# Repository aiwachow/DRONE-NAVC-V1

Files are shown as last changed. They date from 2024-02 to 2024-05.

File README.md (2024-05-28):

# NAVIGATION CONTROL SYSTEM - TEST BOARD 
STM32 based flight controller for unmanned drone aircraft. <br />
Created mainly for testing and learning to write firmware. 

I am simultaneously designing a newer version of this controller: branch NAVC_V2. 

## Board
SYSTEM_KONTROLI_LOTU
## Used software: 
kicadlogo stm32cubeideLOGOpythonLOGO

## Visualization 
I also made basic 3D attitude visualization in Python. 
dronPitch

dronRoll
### Some theory behind attitude estimation in Polish 
[Attitude_Estimation_Theory_Adam_Iwachów.pdf](https://github.com/aiwachow/DRONE-NAVC-V1/files/14794682/Attitude_Estimation_Theory_Adam_Iwachow.pdf)

## Issues 
Pcb has been manufactured and tested. However this design isn't perfect. the main issues are: <br />
- PCB is quite too large, 
- selected microcontroller is difficult to access and was finally changed to STM32L4 .

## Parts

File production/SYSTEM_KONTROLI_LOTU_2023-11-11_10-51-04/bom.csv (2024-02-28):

Designator | Footprint | Quantity | Value | LCSC Part #
BT1 | BatteryHolder_Keystone_1060_1x2032 | 1 | CR2032
C1 | C101 | C102 | C103 | C104 | C105 | C109 | C130 | C140 | C2 | C3 | C302 | C304 | C402 | C403 | C408 | C410 | C411 | C413 | C415 | C416 | C417 | C5 | C501 | C502 | C6 | 0402 | 26 | 100n | C307331
C106 | C4 | C412 | C504 | 0603 | 4 | 4u7 | C19666
C107 | C108 | C301 | C409 | 0603 | 4 | 2u2 | C23630
C110 | C406 | 0402 | 2 | 1u | C52923
C111 | C120 | 0402 | 2 | 12pF | C1547
C401 | 0603 | 1 | 10u | C96446
C407 | 0402 | 1 | 10n | C15195
C418 | 0402 | 1 | 220n | C16772
C503 | 0603 | 1 | 1u | C15849
D1 | 0402 | 1 | 5.5V|6V|15V
D10 | D11 | D2 | D201 | D4 | D9 | 0402 | 6 | 5.5V|6V|14V
D102 | 0603 | 1 | LED_WHITE | C2290
D103 | 0603 | 1 | LED_RED | C2286
D3 | 0603 | 1 | LED_EMERALD | C72043
D7 | 0603 | 1 | LED_BLUE | C72041
D8 | D_SOD-323 | 1 | D_Schottky | C191023
FB2 | 0603 | 1 | 450m|600@100 | C1002
FB3 | 0603 | 1 | 100m|120@100MHz
H1 | H2 | H3 | MountingHole_2.7mm_Pad_Via | 3 | MountingHole
H4 | MountingHole_2.7mm_Pad_Via | 1 | MountingHole_Pad
HM-BT4052 | HM-BT4052 | 1 | ~
IC1 | SOIC127P600X175-8N | 1 | M24128-BFMN6TP
IC2 | QFP50P1200X1200X160-64N_newft | 1 | STM32H562RGT6
IC3 | QMC5883L | 1 | QMC5883L
IC6 | IIM42352 | 1 | ICM-42688-P | C1850418
IC8 | ATGM336H5N31 | 1 | SIM68M|ATGM336H
IC9 | BMI088 | 1 | BMI088 | C194919
J1 | J13 | J4 | J6 | PinHeader_1x03_P2.54mm_Vertical | 4 | Conn_01x03
J10 | DM3CSSF | 1 | DM3CS-SF
J11 | ZX62DB5PA830 | 1 | USB_B_Micro
J12 | UFLRSMT180 | 1 | U.FL-R-SMT-1_80_
J14 | USB_C_Receptacle_GCT_USB4105-xx-A_16P_TopMnt_Horizontal | 1 | USB_C_Receptacle_USB2.0
J16 | PinHeader_1x02_P2.54mm_Vertical | 1 | 5Vin
J3 | PinHeader_1x08_P2.54mm_Vertical | 1 | Conn_01x08
J5 | PinHeader_1x04_P2.54mm_Vertical | 1 | EXTERNAL USART
J7 | PinHeader_1x02_P2.54mm_Vertical | 1 | Conn_I2C3
J8 | PinHeader_1x04_P2.54mm_Vertical | 1 | Conn_01x04
J9 | PinHeader_1x02_P2.54mm_Vertical | 1 | Conn_01x02
JP1 | JP2 | JP3 | JP5 | JP6 | JP7 | JP8 | JP9 | SolderJumper-2_P1.3mm_Open_TrianglePad1.0x1.5mm | 8 | SolderJumper_2_Open
JP4 | PinHeader_1x02_P2.54mm_Vertical | 1 | Jumper_2_Open
L2 | 0603 | 1 | 27n|47n
Q2 | SOT-23 | 1 | NPN | C20526
R1 | 0402 | 1 | 100k | C25741
R101 | R207 | R208 | R209 | R307 | R401 | R402 | 0402 | 7 | 47 | C25092
R103 | R104 | 0603 | 2 | 2k2 | C4190
R105 | R2 | R211 | R3 | R302 | R303 | R304 | R305 | R306 | R408 | R409 | 0402 | 11 | 10k | C25744
R201 | R202 | R203 | R204 | 0402 | 4 | 4k7 | C25900
R205 | R206 | R215 | R216 | R217 | R218 | R219 | 0402 | 7 | 470 | C25117
R210 | R502 | R503 | 0402 | 3 | 5k1 | C25905
R212 | R213 | R214 | R403 | 0402 | 4 | 10 | C25077
R301 | 0402 | 1 | 1M | C26083
R406 | 0402 | 1 | 2k2 | C4190
R407 | R501 | 0603 | 2 | 1k | C21190
SW1 | SW_Push_1P1T_NO_6x6mm_H9.5mm | 1 | NRST
SW4 | SW_Push_1P1T_NO_6x6mm_H9.5mm | 1 | USER_BUTT
TP1 | TP2 | TestPoint_Loop_D1.80mm_Drill1.0mm_Beaded | 2 | TestPoint
U1 | ST_HLGA-10_2x2mm_P0.5mm_LayoutBorder3x2y | 1 | LPS22HB | C94049
U10 | SOT-223-3_TabPin2 | 1 | LDL1117S33R
U2 | Bosch_LGA-8_2x2.5mm_P0.65mm_ClockwisePinNumbering | 1 | SPL06 | C2684428
U7 | SOT-23-6 | 1 | USBLC6-2SC6
Y1 | Crystal_SMD_3225-4Pin_3.2x2.5mm | 1 | HSE_25MHz|12pF | C9006

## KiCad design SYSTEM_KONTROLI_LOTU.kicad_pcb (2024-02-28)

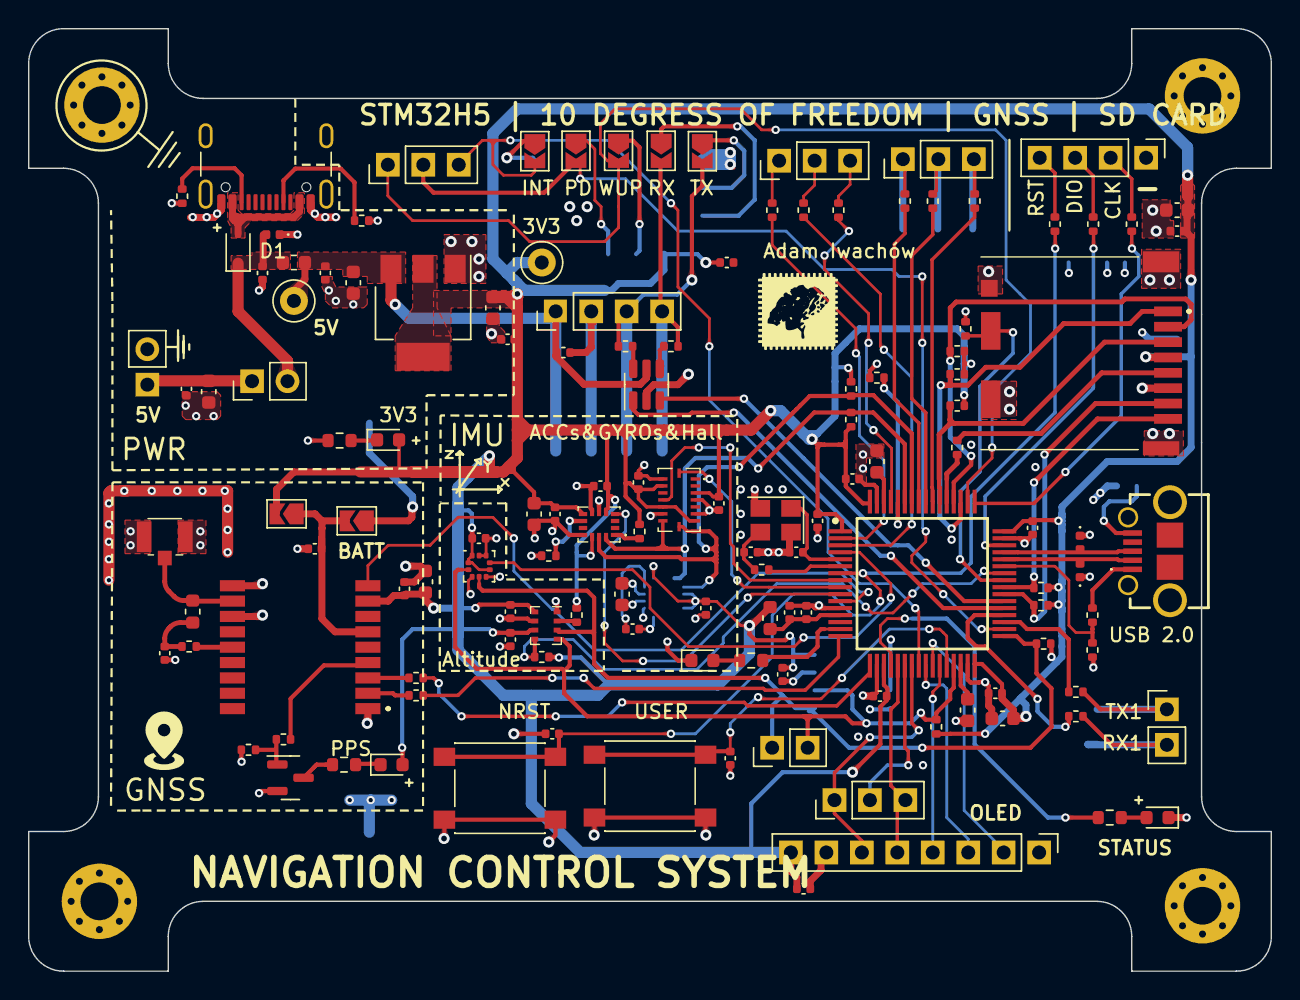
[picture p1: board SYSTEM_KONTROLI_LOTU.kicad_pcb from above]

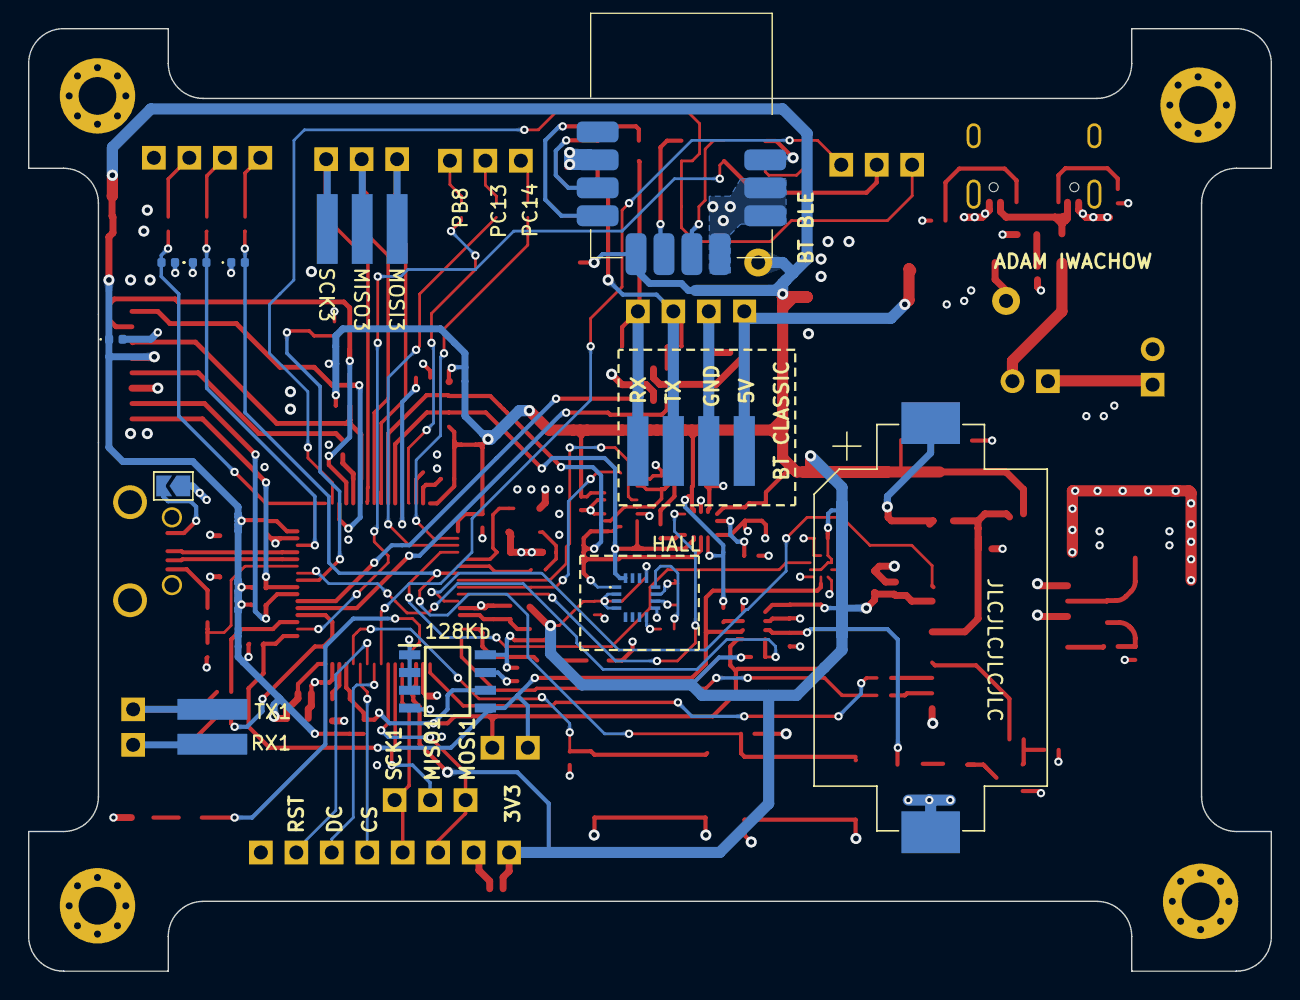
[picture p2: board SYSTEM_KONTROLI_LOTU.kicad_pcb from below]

Board: 4 copper layers, 89.0 x 67.5 mm, 145 parts (9 on the bottom side), 104 nets.

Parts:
BT1: CR2032; BatteryHolder_Keystone_1060_1x2032
C1, C2, C3, C5, C6, C101, C102, C103, C104, C105, C109, C130, C140, C302, C304, C402, C403, C408, C410, C411, C413, C415, C416, C417, C501, C502: 100n; C_0402_1005Metric
C4, C106, C412, C504: 4u7; C_0603_1608Metric
C107, C108, C301, C409: 2u2; C_0603_1608Metric
C110, C406: 1u; C_0402_1005Metric
C111, C120: 12pF; C_0402_1005Metric
C401: 10u; C_0603_1608Metric
C407: 10n; C_0402_1005Metric
C418: 220n; C_0402_1005Metric
C503: 1u; C_0603_1608Metric
D1: 5.5V|6V|15V; D_0402_1005Metric
D2, D4, D9, D10, D11, D201: 5.5V|6V|14V; D_0402_1005Metric
D3: LED_EMERALD; D_0603_1608Metric
D7: LED_BLUE; D_0603_1608Metric
D8: D_Schottky; D_SOD-323
D102: LED_WHITE; D_0603_1608Metric
D103: LED_RED; D_0603_1608Metric
FB2: 450m|600@100; L_0603_1608Metric
FB3: 100m|120@100MHz; L_0603_1608Metric
H1, H2, H3: MountingHole; MountingHole_2.7mm_Pad_Via
H4: MountingHole_Pad; MountingHole_2.7mm_Pad_Via
HM-BT4052: HM-BT4052
IC1: M24128-BFMN6TP; SOIC127P600X175-8N
IC2: STM32H562RGT6; QFP50P1200X1200X160-64N_newft
IC3: QMC5883L
IC6: ICM-42688-P; IIM42352
IC8: SIM68M|ATGM336H; ATGM336H5N31
IC9: BMI088
J1, J4, J6, J13: Conn_01x03; PinHeader_1x03_P2.54mm_Vertical
J3: Conn_01x08; PinHeader_1x08_P2.54mm_Vertical
J5: EXTERNAL USART; PinHeader_1x04_P2.54mm_Vertical
J7: Conn_I2C3; PinHeader_1x02_P2.54mm_Vertical
J8: Conn_01x04; PinHeader_1x04_P2.54mm_Vertical
J9: Conn_01x02; PinHeader_1x02_P2.54mm_Vertical
J10: DM3CS-SF; DM3CSSF
J11: USB_B_Micro; ZX62DB5PA830
J12: U.FL-R-SMT-1_80_; UFLRSMT180
J14: USB_C_Receptacle_USB2.0; USB_C_Receptacle_GCT_USB4105-xx-A_16P_TopMnt_Horizontal
J16: 5Vin; PinHeader_1x02_P2.54mm_Vertical
JP1, JP2, JP3, JP5, JP6, JP7, JP8, JP9: SolderJumper_2_Open; SolderJumper-2_P1.3mm_Open_TrianglePad1.0x1.5mm
JP4: Jumper_2_Open; PinHeader_1x02_P2.54mm_Vertical
L2: 27n|47n; L_0603_1608Metric
Q2: NPN; SOT-23
R1: 100k; R_0402_1005Metric
R2, R3, R105, R211, R302, R303, R304, R305, R306, R408, R409: 10k; R_0402_1005Metric
R101, R207, R208, R209, R307, R401, R402: 47; R_0402_1005Metric
R103, R104: 2k2; R_0603_1608Metric
R201, R202, R203, R204: 4k7; R_0402_1005Metric
R205, R206, R215, R216, R217, R218, R219: 470; R_0402_1005Metric
R210, R502, R503: 5k1; R_0402_1005Metric
R212, R213, R214, R403: 10; R_0402_1005Metric
R301: 1M; R_0402_1005Metric
R406: 2k2; R_0402_1005Metric
R407, R501: 1k; R_0603_1608Metric
SW1: NRST; SW_Push_1P1T_NO_6x6mm_H9.5mm
SW4: USER_BUTT; SW_Push_1P1T_NO_6x6mm_H9.5mm
TP1, TP2: TestPoint; TestPoint_Loop_D1.80mm_Drill1.0mm_Beaded
U1: LPS22HB; ST_HLGA-10_2x2mm_P0.5mm_LayoutBorder3x2y
U2: SPL06; Bosch_LGA-8_2x2.5mm_P0.65mm_ClockwisePinNumbering
U7: USBLC6-2SC6; SOT-23-6
U10: LDL1117S33R; SOT-223-3_TabPin2
Y1: HSE_25MHz|12pF; Crystal_SMD_3225-4Pin_3.2x2.5mm

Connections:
+3.3V: C1.1, C3.1, C6.1, C101.1, C102.1, C103.1, C104.1, C105.1, C106.1, C301.1, C302.1, C304.1, C401.1, C402.1, C407.1, C408.1, C409.1, C410.1, C411.1, C413.1, C415.1, C416.1, C417.1, C504.1, D3.2 (A), D7.2 (A), D9.1 (A1), FB2.1, HM-BT4052.7 (VDD), IC1.8 (VCC), IC2.1 (VBAT), IC2.19 (VDD_1), IC2.32 (VDD_2), IC2.48 (VDD_3), IC2.64 (VDD_4), IC3.2 (VDD), IC3.4 (S1), IC3.13 (VDDIO), IC6.5 (VDDIO), IC6.8 (VDD), IC6.12 (VDDIO), IC8.8 (VCC), IC9.3 (VDD), IC9.7 (PS), IC9.11 (VDDIO), IC9.14 (CSB1), J3.8, J10.4 (VDD), JP3.2 (B), R2.2, R3.2, R201.2, R202.2, R203.2, R204.2, R302.2, R303.2, R304.2, R305.2, R306.2, R409.1, TP2.1, U1.1 (Vdd_IO), U1.6 (~CS), U1.10 (VDD), U2.6 (Vdd_IO), U2.8 (VDD), U10.2 (VO)
+3.3VA: C109.1, C110.1, FB2.2, IC2.13 (VDDA)
+5V: C5.2, C502.1, C503.1, FB3.2, J5.1, TP1.1, U7.5 (VBUS), U10.3 (VI)
/NAVC_STM32 /NAVC_CONNECTORS/bT_INT: HM-BT4052.1 (INT), JP6.1 (A)
/NAVC_STM32 /NAVC_CONNECTORS/bT_PDN: HM-BT4052.5 (PDN), JP5.1 (A)
/NAVC_STM32 /NAVC_CONNECTORS/bT_WP: HM-BT4052.6 (WAKEUP), JP2.1 (A)
/NAVC_STM32 /NAVC_CONNECTORS/nAVC_MCS_INT2_PB8: J6.3, R217.1
/NAVC_STM32 /NAVC_CONNECTORS/nAVC_MCS_INT2_PC13: J6.1, R215.1
/NAVC_STM32 /NAVC_CONNECTORS/nAVC_MCS_INT2_PC14: J6.2, R216.1
/NAVC_STM32 /NAVC_CONNECTORS/nRST: J8.4, R207.1
/NAVC_STM32 /NAVC_CONNECTORS/sPI3_MISO: J13.2, R213.1
/NAVC_STM32 /NAVC_CONNECTORS/sPI3_MOSI: J13.1, R214.1
/NAVC_STM32 /NAVC_CONNECTORS/sPI3_SCK: J13.3, R212.1
/NAVC_STM32 /NAVC_CONNECTORS/sWCLK: J8.2, R208.2
/NAVC_STM32 /NAVC_CONNECTORS/sWDIO: J8.3, R209.2
/NAVC_STM32 /NAVC_CONNECTORS/uSART1_RX: J9.2, R218.2
/NAVC_STM32 /NAVC_CONNECTORS/uSART1_TX: J9.1, R219.2
/NAVC_STM32 /NAVC_CONNECTORS/usART6_RX: HM-BT4052.8 (UART_RXD), JP8.1 (A)
/NAVC_STM32 /NAVC_CONNECTORS/usART6_TX: HM-BT4052.9 (UART_TXD), JP7.1 (A)
/NAVC_STM32 /NAVC_MEMORY/sDMMC1_CLK: J10.5 (CLK), R307.2
/NAVC_STM32 /NAVC_POWER/5Vin: C2.1, C4.1, J16.1, JP4.1 (A)
/NAVC_STM32 /NAVC_POWER/Vusb: D8.2 (A), J14.A4 (VBUS), J14.A9 (VBUS), J14.B4 (VBUS), J14.B9 (VBUS)
/NAVC_STM32 /NAVC_SENSORS/antenna: IC8.11 (RF_IN), J12.1 (SIG), L2.2
/NAVC_STM32 /NAVC_SENSORS/uSART2_RX_GNSS: IC8.3 (RXD), R402.2
/NAVC_STM32 /NAVC_SENSORS/uSART2_TX_GNSS: IC8.2 (TXD), R401.2
/NAVC_STM32 /hSE_OUT: C120.1, R101.1, Y1.3
BACKUP: C406.1, IC8.6 (V_BCKP), JP1.2 (B), JP3.1 (A)
BMI088_INT1_ACC: IC2.9 (PC1), IC9.16 (INT1)
BMI088_INT3_GYRO: IC2.8 (PC0), IC9.12 (INT3)
BOOT0: IC2.60 (BOOT0), R105.1
BT_INT_PC4: IC2.24 (PC4), J1.3, JP6.2 (B)
BT_PDN_PB13: IC2.34 (PB13), J1.2, JP5.2 (B)
BT_WAKEUP_PA15: IC2.50 (PA15), J1.1, JP2.2 (B)
CARD_DETECT: IC2.41 (PA8), J10.10 (CARD_D), R301.2
CC1: J14.A5 (CC1), R502.1
CC2: J14.B5 (CC2), R503.1
GND: BT1.2 (-), C1.2, C2.2, C3.2, C4.2, C5.1, C6.2, C101.2, C102.2, C103.2, C104.2, C105.2, C106.2, C107.2, C108.2, C109.2, C110.2, C111.2, C120.2, C130.1, C140.1, C301.2, C302.2, C304.2, C401.2, C402.2, C403.2, C406.2, C407.2, C408.2, C409.2, C410.2, C411.2, C412.2, C413.2, C415.2, C416.2, C417.2, C501.2, C502.2, C503.2, C504.2, D1.1 (A1), D2.1 (A1), D4.1 (A1), D9.2 (A2), D10.1 (A1), D11.1 (A1), D102.1 (K), D103.1 (K), D201.1 (A1), H4.1, HM-BT4052.2 (GND), HM-BT4052.3 (GND), HM-BT4052.4 (GND), HM-BT4052.10 (GND), IC1.1 (E0), IC1.2 (E1), IC1.3 (E2), IC1.4 (VSS), IC1.7 (~WC), IC2.12 (VSSA), IC2.18 (VSS_1), IC2.31 (VSS_2), IC2.47 (VSS_3), IC2.63 (VSS_4), IC3.9 (GND_1), IC3.11 (GND_2), IC6.6 (GND), IC6.7 (RESV_3), IC6.11 (RESV_5), IC8.1 (GND), IC8.10 (GND), IC8.12 (GND), IC9.4 (GNDA), IC9.6 (GNDIO), IC9.10 (SDO2), IC9.15 (SDO1), J3.7, J5.2, J8.1, J10.6 (VSS), J10.9 (GND), J10.11 (GND), J10.12 (GND), J10.13 (GND), J12.2 (GND_1), J12.3 (GND_2), J14.A1 (GND), J14.A12 (GND), J14.B1 (GND), J14.B12 (GND), J16.2, JP9.1 (A), Q2.2 (E), R1.1, R105.2, R211.1, R301.1, R408.1, R501.1, R502.2, R503.2, SW1.3 (B), SW4.3 (B), U1.3 (RES), U1.5 (SA0), U1.8 (GND), U1.9 (GND), U2.1 (GND), U2.7 (GND), U7.2 (GND), U10.1 (GND), Y1.2, Y1.4
GNSS_NRST: IC2.11 (PC3), IC8.9 (RESET_N)
HSE_IN: C111.1, IC2.5 (PH0-OSC_IN), Y1.1
HSE_OUT: IC2.6 (PH1-OSC_OUT), R101.2
I2C1_SCK: IC2.58 (PB6), IC3.1 (SCL), IC6.13 (SCK), IC9.8 (SCL/SCK), R202.1
I2C1_SDA: IC2.59 (PB7), IC3.16 (SDA), IC6.14 (SDA), IC9.9 (SDA/SDI), R201.1
I2C2_SCK: IC1.6 (SCL), IC2.29 (PB10), J7.2, R204.1, U1.2 (SCL), U2.4 (SCL)
I2C2_SDA: IC1.5 (SDA), IC2.33 (PB12), J7.1, R203.1, U1.4 (SDA), U2.3 (SDA)
ICM_INT1: IC2.10 (PC2), IC6.4 (INT1_/_INT)
LED2: IC2.15 (PA1), R103.2
LED3: IC2.20 (PA4), R104.2
LPS22_DRDY: IC2.4 (PC15-OSC32_OUT), U1.7 (INT_DRDY)
NAVC_MCS_INT1_PC14: IC2.3 (PC14-OSC32_IN), R216.2
NAVC_MCS_INT2_PC13: IC2.2 (PC13), R215.2
NAVC_MCS_INT3_PB8: IC2.61 (PB8), R217.2
NRST: C130.2, D201.2 (A2), IC2.7 (NRST), R207.2, SW1.1 (A)
unnamed: BT1.1 (+), JP1.1 (A)
unnamed: C403.1, L2.1, R403.2
unnamed: D3.1 (K), R501.2
unnamed: D7.1 (K), R407.2
unnamed: D102.2 (A), R103.1
unnamed: D103.2 (A), R104.1
unnamed: C412.1, IC3.10 (C1)
unnamed: C418.2, IC3.12 (SETC)
unnamed: C418.1, IC3.8 (STEP)
unnamed: IC6.1 (AP_SDO), R409.2
unnamed: IC6.9 (INT2), R408.2
unnamed: IC8.14 (VCC_RF), R403.1
unnamed: J11.5 (GND), JP9.2 (B)
unnamed: J11.1 (VBUS), R210.1
unnamed: Q2.1 (B), R1.2, R406.2
unnamed: Q2.3 (C), R407.1
unnamed: R205.1, U7.4 (I/O2)
unnamed: R206.1, U7.6 (I/O1)
unnamed: R3.1, U2.2 (~CS)
OLED_CS: IC2.27 (PB1), J3.4
OLED_DC: IC2.25 (PC5), J3.3
OLED_RST: IC2.26 (PB0), J3.2
SDMMC1_CLK: IC2.53 (PC12), R307.1
SDMMC1_CMD: IC2.54 (PD2), J10.3 (CMD), R302.1
SDMMC1_D0: IC2.39 (PC8), J10.7 (DAT0), R303.1
SDMMC1_D1: IC2.40 (PC9), J10.8 (DAT1), R304.1
SDMMC1_D2: IC2.51 (PC10), J10.1 (DAT2), R305.1
SDMMC1_D3: IC2.52 (PC11), J10.2 (CD/DAT3), R306.1
SLP_INT: IC2.42 (PA9), R2.1, U2.5 (SD0)
SPI1_MISO: IC2.22 (PA6), J4.2
SPI1_MOSI: IC2.23 (PA7), J3.6, J4.1
SPI1_SCK: IC2.21 (PA5), J3.5, J4.3
SPI3_MISO: IC2.56 (PB4), R213.2
SPI3_MOSI: IC2.57 (PB5), R214.2
SPI3_SCK: IC2.55 (PB3), R212.2
SWCLK: D4.2 (A2), IC2.49 (PA14), R208.1
SWDIO: D2.2 (A2), IC2.46 (PA13), R209.1
TIMEMARK: IC8.4 (1PPS), R406.1
USART1_RX: IC2.36 (PB15), R218.1
USART1_TX: IC2.35 (PB14), R219.1
USART2_RX_GNSS: IC2.17 (PA3), R402.1
USART2_TX_GNSS: IC2.16 (PA2), R401.1
USART6_RX: IC2.38 (PC7), U7.3 (I/O2)
USART6_TX: IC2.37 (PC6), U7.1 (I/O1)
USB_DN: D11.2 (A2), IC2.44 (PA11), J11.2 (D-)
USB_DP: D10.2 (A2), IC2.45 (PA12), J11.3 (D+)
USB_OTG_STAT: IC2.43 (PA10), R210.2, R211.2
USER_BUTT: C140.2, IC2.28 (PB2), SW4.1 (A)
VBUS: C501.1, D1.2 (A2), D8.1 (K), FB3.1, JP4.2 (B)
Vcap: C107.1, C108.1, IC2.30 (VCAP_1), IC2.62 (VCAP_2)
uSART6_RX: J5.4, JP8.2 (B), R205.2
uSART6_TX: J5.3, JP7.2 (B), R206.2

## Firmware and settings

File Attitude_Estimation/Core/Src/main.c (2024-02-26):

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
/* Includes ------------------------------------------------------------------*/
#include "main.h"
#include "i2c.h"
#include "tim.h"
#include "usart.h"
#include "gpio.h"

/* USER CODE BEGIN Includes */
#include "I2C_BusMonitor.h"
#include "Altimeter.h"
#include "QMC5883L.h"
#include "BMI088.h"
#include "LPS25HB_I2C.h"
#include "ICM_42688_P.h"
#include "SPL06.h"
#include "RollPitchYaw.h"
#include <stdio.h>
#include <SPL06.h>
#include <string.h>
/* USER CODE END Includes */

/* USER CODE BEGIN PD */
#define SAMPLE_RATE 50
#define MAGNETOMETER_ON   1
#define MAGNETOMETER_OFF  2
#define ALTIMETER_ON  	  2
#define ALTIMETER_OFF     1

/* USER CODE END PD */


/* USER CODE BEGIN PV */

typedef struct{

	LPS25HB_t 	LPS25;
	SPL06_t   	SPL;
	Altimeter_t Altimeter;
	ICM_42688_t IMC;
	BMI088_t 	BMI;
	QMC5883L_t 	QMC;

}Device_t;


Device_t Dev;


RollPitchYaw_t RPY_dev;

float Rad_to_Deg = 57.295f;


float GRAVITY_EARTH = 9.81;
uint8_t DataReadyBMIGyro = 0;
uint8_t DataReadyBMIAcc = 0;
uint8_t DataReadySPL = 0;
uint8_t DataReadyLPS25 = 0;

volatile float AverageTemp = 0.0f;

uint32_t time_tick = 0, Sample_time = 25;

volatile uint8_t ALTIcounter = 0;
volatile uint8_t MAGcounter = 0;
uint8_t ALTI_ON = 0;
uint8_t MAG_ON = 0;


// Filter coefficients
//float ALPHA_ACC
//float ALPHA_GYRO	0.8f
//float ALPHA_MAG 	0.5f

/* USER CODE END PV */

void SystemClock_Config(void);
/* USER CODE BEGIN 0 */

int __io_putchar(int ch)
{
  if (ch == '\n') {
    __io_putchar('\r');
  }

  HAL_UART_Transmit(&huart1, (uint8_t*)&ch, 1, HAL_MAX_DELAY);

  return 1;
}

void HAL_GPIO_EXTI_Callback(uint16_t GPIO_Pin)
{


	if(GPIO_Pin == BMI_GYRO_INT_Pin){
	//	 DataReadyBMIGyro = 1;
		}
	if(GPIO_Pin == BMI_ACC_INT_Pin){
	//DataReadyBMIAcc = 1;
			}
	if(GPIO_Pin == SPL_INT_Pin){
		//DataReadySPL = 1;
	}
	if(GPIO_Pin == LPS25_INT_Pin){
		//DataReadyLPS25 = 1;

	}

	if(GPIO_Pin == USER_BUTT_Pin){

		ALTIcounter++;
		MAGcounter++;

		if(ALTIcounter >= ALTIMETER_ON){
			HAL_TIM_OC_Stop_IT(&htim4, TIM_CHANNEL_1);

			MAGcounter = 0;
			ALTIcounter = 0;
			ALTI_ON ^= 1;

			HAL_GPIO_TogglePin(Sensors_Led_GPIO_Port,  Sensors_Led_Pin);



		}
		else if(ALTIcounter ==  ALTIMETER_OFF){
			HAL_TIM_OC_Start_IT(&htim4, TIM_CHANNEL_1);
		}

	}



}


void HAL_TIM_OC_DelayElapsedCallback(TIM_HandleTypeDef *htim)
{
  if (htim == &htim4) {
    switch (HAL_TIM_GetActiveChannel(&htim4)) {
    case HAL_TIM_ACTIVE_CHANNEL_1:

    	ALTIcounter = 0;

    	if(MAGcounter == MAGNETOMETER_ON){
    		MAG_ON ^= 1;
    		HAL_GPIO_TogglePin(Status_Led_GPIO_Port,  Status_Led_Pin);
    		MAGcounter = 0;

    	}
    	HAL_TIM_OC_Stop_IT(&htim4, TIM_CHANNEL_1);

      break;

    default:
      break;
    }
  }
  if (htim == &htim3) {
    switch (HAL_TIM_GetActiveChannel(&htim3)) {
    case HAL_TIM_ACTIVE_CHANNEL_1:
    	//Some troubles on I2C bus sensor led blinking with 1Hz
      HAL_GPIO_TogglePin(Sensors_Led_GPIO_Port,  Sensors_Led_Pin);
      break;
    case HAL_TIM_ACTIVE_CHANNEL_2:
    	//Some critical troubles on I2C bus sensor led blinking with 2Hz
      HAL_GPIO_TogglePin(Sensors_Led_GPIO_Port,  Sensors_Led_Pin);
      break;
    case HAL_TIM_ACTIVE_CHANNEL_3:
    	// No I2C devices status blinking with 4Hz
        HAL_GPIO_TogglePin(Status_Led_GPIO_Port,  Status_Led_Pin);
        break;
    default:
      break;
    }
  }
}


/* USER CODE END 0 */

/**
  * @brief  The application entry point.
  * @retval int
  */
int main(void)
{
  /* MCU Configuration--------------------------------------------------------*/

  /* Reset of all peripherals, Initializes the Flash interface and the Systick. */
  HAL_Init();

  /* Configure the system clock */
  SystemClock_Config();

  /* Initialize all configured peripherals */
  MX_GPIO_Init();
  MX_I2C1_Init();
  MX_USART2_UART_Init();
  MX_I2C2_Init();
  MX_TIM3_Init();
  MX_TIM4_Init();
  MX_USART1_UART_Init();
  /* USER CODE BEGIN 2 */
 // HAL_I2C_EnableListen_IT(&hi2c1);
ScanI2CBus(&hi2c1); ScanI2CBus(&hi2c2);
CheckI2Cfaults(SPL06_INIT(&Dev.SPL, &hi2c1, SPL06_I2C_ADDRESS_I));
CheckI2Cfaults(BMI088_INIT(&Dev.BMI, &hi2c2));
CheckI2Cfaults(QMC5883L_INIT(&Dev.QMC,&hi2c1 , QMC5883L_ADDRESS));


// dummy read
QMC5883L_ReadMag(&Dev.QMC, 0.5f);
SPL06_READ_TEMP_PRESS(&Dev.SPL);
BMI088_ReadAcc(&Dev.BMI); BMI088_ReadGyro(&Dev.BMI);

INIT_ALTIMETER(&Dev.Altimeter, Dev.SPL.pressure_hPa);
DataPrepareForAlitmeter(&Dev.Altimeter,&Dev.SPL, 50);

InitRollPitchYawEstimationFunc(&RPY_dev);

  /* USER CODE END 2 */

  /* Infinite loop */
  /* USER CODE BEGIN WHILE */
  while (1)
{


	  if(HAL_GetTick() - time_tick >= Sample_time)
	 	  {

		  time_tick = HAL_GetTick();

		  BMI088_ReadAcc(&Dev.BMI);
		  BMI088_ReadGyro(&Dev.BMI);
		  QMC5883L_ReadMag(&Dev.QMC, 0.6f);
		  SPL06_READ_TEMP_PRESS(&Dev.SPL);
		  Estimate_Altitude(&Dev.Altimeter ,&Dev.SPL,Dev.SPL.pressure_hPa, Dev.SPL.temp_cel,1);
		  EstimateRollPitchYawComplementaryFilter(&RPY_dev, &Dev.BMI,&Dev.QMC,0.1f,0.8f,Sample_time , 0.1f, ALTI_ON);

		  printf("%.3f,%.3f,%.3f,%.3f,%d,%d\n",RPY_dev.RollAngle , RPY_dev.PitchAngle,RPY_dev.YawAngle,Dev.Altimeter.Altitude_1, ALTI_ON, MAG_ON);



	  }






    /* USER CODE END WHILE */

    /* USER CODE BEGIN 3 */
}
  /* USER CODE END 3 */
}

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


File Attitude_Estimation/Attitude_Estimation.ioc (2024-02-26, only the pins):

Mcu.UserName=STM32L476RGTx
PA10.Signal=USART1_RX
PA2.Signal=USART2_TX
PA3.Signal=USART2_RX
PA9.Signal=USART1_TX
PB10.GPIO_Label=Sensors_Led
PB10.Signal=GPIO_Output
PB11.GPIO_Label=Status_Led
PB11.Signal=GPIO_Output
PB13.Signal=I2C2_SCL
PB14.Signal=I2C2_SDA
PB8.Signal=I2C1_SCL
PB9.Signal=I2C1_SDA
PC1.GPIO_Label=SPL_INT
PC1.Signal=GPXTI1
PC11.GPIO_Label=LPS25_INT
PC11.Signal=GPXTI11
PC2.GPIO_Label=BMI_ACC_INT
PC2.Signal=GPXTI2
PC3.GPIO_Label=BMI_GYRO_INT
PC3.Signal=GPXTI3
PC9.GPIO_Label=USER_BUTT
PC9.Signal=GPXTI9

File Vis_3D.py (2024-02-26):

from vpython import *
from time import *
import numpy as np
import math

import serial
import time

STM32L4 = serial.Serial('com8', 115200)
time.sleep(1)

scene_3d = canvas(background=color.white, width=1200, height=300)
scene_3d.axis = vector(0,0.8,-1)

x = 0
start_time = time.time()

# Two coordinate systems, Body-Fixed Frame 1, Inertial Frame 2
axisX1 = arrow(length=0.5, pos=vector(0, 0, -0.5), axis=vector(1, 0, 0), color=color.red, shaftwidth=0.05)
axisY1 = arrow(length=0.5, pos=vector(0, 0,  -0.5), axis=vector(0, 1, 0), color=color.green, shaftwidth=0.05)
axisZ1 = arrow(length=0.5, pos=vector(0, 0,  -0.5), axis=vector(0, 0, 1), color=color.blue, shaftwidth=0.05)

axisX2 = arrow(length=1.5, pos=vector(0, 0, -0.5), axis=vector(1, 0, 0), color=color.cyan, shaftwidth=0.05)
axisY2 = arrow(length=1.5, pos=vector(0, 0, -0.5), axis=vector(0.5, 1, 0), color=color.magenta, shaftwidth=0.05)
axisZ2 = arrow(length=1.5, opacity = 0.5,pos=vector(0, 0, -0.5), axis=vector(0, 0, 1), color=color.yellow, shaftwidth=0.05)


# Pseudo drone model 
corpus = box(pos=vector(0, 0, 0), size=vector(1, 0.5, 0.1), color=color.black)

prostopadloscian1 = box(pos=corpus.pos, size=vector(2, 0.1, 0.1),
                        axis=vector(1, 1, 0), color=color.black)
prostopadloscian2 = box(pos=corpus.pos, size=vector(2, 0.1, 0.1),
                        axis=vector(1, -1, 0), color=color.black)
walec1 = cylinder(pos=prostopadloscian1.pos + vector(0.7, 0.7, 0), axis=vector(0, 0, 0.1),
                  radius=0.2, color=color.black)
walec2 = cylinder(pos=prostopadloscian2.pos + vector(-0.7, -0.7, 0), axis=vector(0, 0, 0.1),
                  radius=0.2, color=color.black)
walec3 = cylinder(pos=prostopadloscian1.pos + vector(-0.7, 0.7, 0), axis=vector(0, 0, 0.1),
                  radius=0.2, color=color.black)
walec4 = cylinder(pos=prostopadloscian2.pos + vector(0.7, -0.7, 0), axis=vector(0, 0, 0.1),
                  radius=0.2, color=color.black)

Dron = compound([corpus, prostopadloscian1, prostopadloscian2, walec1, walec2, walec3, walec4])
Dron.pos = vector(0, 0, -0.5)
Dron.opacity = 0.5

# labels 
label(pos=axisX2.axis + vector(0, 0, 0), text='X', height=10, box=False)
label(pos=axisY2.axis + vector(0, 0.1, 0), text='Y', height=10, box=False)
label(pos=axisZ2.axis + vector(0, 0, 0.1), text='Z', height=10, box=False)

# text labels 
roll_pitch_label = label(pos=vector(3.5, -1, 0) , height=15, box=False)


graph_height = 200
graph_spacing = 20
graph_width = 295

# Roll
graph1 = graph(title='Roll (deg)', align='left', width=graph_width, height=graph_height)
plot1 = gcurve(graph=graph1, color=color.red)

# Pitch
graph2 = graph(title='Pitch (deg)', align='left', width=graph_width, height=graph_height)
plot2 = gcurve(graph=graph2, color=color.blue)

# Yaw
graph3 = graph(title='Yaw (deg)', align='left', width=graph_width, height=graph_height)
plot3 = gcurve(graph=graph3, color=color.green)

#  Altitude
graph4 = graph(title='Altitude (m)', align='left', width=graph_width, height=graph_height)
plot4 = gcurve(graph=graph4, color=color.black)




while True:
    while STM32L4.inWaiting() == 0:
        pass

    DataPacket  = STM32L4.readline()
    DataPacket  = str(DataPacket, 'utf-8')
    splitPacket = DataPacket.split(',')

    Roll              = float(splitPacket[0]) 
    Pitch             = float(splitPacket[1]) * (-1)
    Yaw               = float(splitPacket[2])
    Altitude          = float(splitPacket[3]) 
    IS_MAG_ON         = float(splitPacket[4])
    DataAnlizeOnOff   = float(splitPacket[5])
    


    # interial frame ZYX
    axisX1.axis = vector(
        cos(Pitch) * cos(Yaw),
        cos(Pitch) * sin(Yaw),
        -sin(Pitch)
    )
    axisX1.length = 1

    axisY1.axis = vector(
        cos(Yaw)*sin(Roll)*sin(Pitch)-cos(Roll)*sin(Yaw),
        cos(Roll)*cos(Yaw) + sin(Roll)*sin(Yaw)*sin(Pitch),
        cos(Pitch)*sin(Roll)
    
    )
    axisZ1.length = 1

    axisZ1.axis = vector(
        sin(Roll)*sin(Yaw)+cos(Roll)*cos(Yaw)*sin(Pitch),
        cos(Roll)*sin(Yaw)*sin(Pitch)-cos(Yaw)*sin(Roll),
        cos(Roll)*cos(Pitch)
         
    )
    
            
    Dron.axis  = axisX1.axis
    Dron.up    = axisY1.axis

   

    elapsed_time = time.time() - start_time
    x = elapsed_time

    axisX1.pos = vector(0,0,Altitude)
    axisY1.pos = vector(0,0,Altitude)
    axisZ1.pos = vector(0,0,Altitude)
    Dron.pos   = vector(0,0,Altitude)
    
    
    rate(100)
    
    if DataAnlizeOnOff == 1:
        plot4.plot(x, Altitude)
        plot1.plot(x, Roll * (180/np.pi))
        plot2.plot(x, Pitch * (180/np.pi))
        plot3.plot(x, Yaw * (180/np.pi))
        plot4.plot(x, Altitude)
        roll_pitch_label.text = f'Roll: {Roll * (180/np.pi):.2f}, Pitch: {Pitch * (180/np.pi):.2f}, Yaw: {Yaw * (180/np.pi):.2f}, Altitude: {Altitude*100:.2f} cm, \nData Analize on: {DataAnlizeOnOff}, Mag on: {IS_MAG_ON}'

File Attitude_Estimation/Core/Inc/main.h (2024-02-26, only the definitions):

#define SPL_INT_Pin GPIO_PIN_1
#define SPL_INT_GPIO_Port GPIOC
#define SPL_INT_EXTI_IRQn EXTI1_IRQn
#define BMI_ACC_INT_Pin GPIO_PIN_2
#define BMI_ACC_INT_GPIO_Port GPIOC
#define BMI_ACC_INT_EXTI_IRQn EXTI2_IRQn
#define BMI_GYRO_INT_Pin GPIO_PIN_3
#define BMI_GYRO_INT_GPIO_Port GPIOC
#define BMI_GYRO_INT_EXTI_IRQn EXTI3_IRQn
#define Sensors_Led_Pin GPIO_PIN_10
#define Sensors_Led_GPIO_Port GPIOB
#define Status_Led_Pin GPIO_PIN_11
#define Status_Led_GPIO_Port GPIOB
#define USER_BUTT_Pin GPIO_PIN_9
#define USER_BUTT_GPIO_Port GPIOC
#define USER_BUTT_EXTI_IRQn EXTI9_5_IRQn
#define LPS25_INT_Pin GPIO_PIN_11
#define LPS25_INT_GPIO_Port GPIOC
#define LPS25_INT_EXTI_IRQn EXTI15_10_IRQn

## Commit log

2024-02-28 adding schematics
    [NAVC_conns.kicad_sch, NAVCmem.kicad_sch, NAVCperiph.kicad_sch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]
2024-02-28 rest of the files
    [SYSTEM_KONTROLI_LOTU.kicad_pcb, bom.csv, designators.csv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]

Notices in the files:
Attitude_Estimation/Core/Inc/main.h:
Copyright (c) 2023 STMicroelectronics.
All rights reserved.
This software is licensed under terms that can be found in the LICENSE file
